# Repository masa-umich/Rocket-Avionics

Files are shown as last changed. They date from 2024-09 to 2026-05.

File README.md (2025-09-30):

# Rocket-Avionics
Embedded firmware for Rocket Avionics

Read Me last updated: 9/2/2025

## Note:
This is a mono-repo meaning that code for the bay boards, flight computer, and all other rocket avionics should go into sub-directories of this repo. The only exception to this is Limewire since that is an interface to the flight computer and not part of rocket avionics itself.

Find all firmware that actually runs on boards in `stm-flight-sw/`

Find all the templates in `stm-templates/`

Sensor Emulation Board (SEB) -> `SEB/`

Apogee Detection Sims & RTOS Threads -> `apogee-detection/`

All on-board driver firmware -> `board-drivers/`

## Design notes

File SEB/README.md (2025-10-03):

# Sesnor Emulation Board Firmware & Software
Author: Jack Hammerberg\
Last updated: 10/2/2025

## Application Notes
* You MUST use hardware NSS when configuring a SPI slave in STM32! The software option will not allow the MISO register to get shifted out
* If re-using the MS5611 emulator code, remember to call `emulation_init()` before your main loop, `emulation_loop(<serial uart>)` in the main loop, and setup SPI interrupts w/ HAL calls disabled and replaced with `emulation_IRQHandler(<spi bus>)`

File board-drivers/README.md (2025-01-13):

# Flight Computer & Bay Board Drivers

## Current Members:
Jack Hammerberg, Felix Foreman, Ryan Salehi

## Summary:
This directory contains all of the relevant drivers used on the rocket avionics firmware. Not every board will use every driver, these drivers are designed to be copy-pasted into each application or project as needed. Most if not all require FreeRTOS to work properly for non-blocking opperation.

## Drivers:
* Name: FCBBADC (Flight Computer & Bay Board Analog to Digital Converter)
* Init ADCs in batch
* Read in batch
* Convert to raw in batch
* Convert to voltages in batch (float32 array)
* Driver Functions:
    * Init
    * Get Raw Values
    * Get Raw Voltages
    * Get Voltages & Timestamps

* MAX11128
    * [MAX11128 Datasheet](https://www.analog.com/media/en/technical-documentation/data-sheets/MAX11120-MAX11128.pdf)
    * Type: ADC
    * Interface: SPI
    * Driver Requirements:
        * Init
        * Send Command
        * Read Register
        * Write Register
        * Get Voltage

* LPS22HBTR 
    * [LPS22HBTR Datasheet](https://www.st.com/content/ccc/resource/technical/document/datasheet/bf/c1/4f/23/61/17/44/8a/DM00140895.pdf/files/DM00140895.pdf/jcr:content/translations/en.DM001408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)
    * Type: Barometer/Altimeter 
    * Interface: SPI
    * Driver Requirements:
        * Init
        * Send Command
        * Read Register
        * Write Register
        * Get Altitude
        * Get Pressure

* LSM6DSO32XTR
    * [LSM6DSO32XTR Datasheet](https://www.st.com/resource/en/datasheet/lsm6dso32x.pdf)
    * Type: IMU
    * Interface: SPI
    * Driver Requirements:
        * Init
        * Send Command
        * Read Register
        * Write Register
        * Get Accelleration
        * Get Angular Rate
        * Get Temperature

* M5611
    * [M5611 Datasheet](https://www.mouser.com/datasheet/2/418/6/ENG_DS_MS5611_01BA03_B3-1134567.pdf)
    * Type: Barometer/Altimeter
    * Interface: SPI
    * Driver Requirements:
        * Init
        * Pressure Convert
        * Temperature Convert
        * Read Pressure
        * Read Temperature

* M24256E
    * [M24256E Datasheet](https://www.st.com/resource/en/datasheet/m24256e-f.pdf)
    * Type: EEPROM 
    * Interace: I2C
    * Driver Requirements:
        * Init
        * Send Command
        * Read Register
        * Write Register
        * Write Flash
        * Read Flash

* NEO-M9N-00B
    * [NEO-M9N-00B](https://content.u-blox.com/sites/default/files/NEO-M9N-00B_DataSheet_UBX-19014285.pdf)
    * Type: GPS
    * Interface: SPI
    * Driver Requirements:
        * Init
        * Send Command
        * Read Register
        * Write Register
        * Get Lat/Long/Alt

* SX1280 
    * [SX1280 Datasheet](https://semtech.my.salesforce.com/sfc/p/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)
    * Type: LoRa 2.4GHz Radio 
    * Interface: SPI
    * Driver Requirements:
        * Init
        * Send Command
        * Read Register
        * Write Register
        * Transmit Data
        * Recieve Data

* W25N01GVZEIG
    * [W25N01GV Datasheet](https://www.winbond.com/resource-files/w25n01gv%20revl%20050918%20unsecured.pdf)
    * Type: Flash 
    * Interface: SPI
    * Driver Requirements:
        * Init
        * Send Command
        * Read Register
        * Write Register
        * Write Flash
        * Read Flash

* ADS1120 
    * [ADS1120 Datasheet](https://www.ti.com/lit/ds/symlink/ads1120.pdf)
    * Type: Thermocouple ADC
    * Interface: SPI
    * Driver Requirements:
        * Init
        * Send Command
        * Read Register
        * Write Register
        * Get Temperature
        * Read All TCs and Attach Timestamps

* Valves
    * Type: Solenoid Valves
    * Interface: GPIO & Shift Register
    * Driver Requirements:
        * Valve Voltage Config (Shift Register)
        * Open Valve
        * Close Valve

* TCP
    * Type: TCP/IP
    * Interface: Ethernet
    * Driver Requirements:
        * Packet Parsing
        * Connection Thread Manager
        * TCP Server
        * TCP Client

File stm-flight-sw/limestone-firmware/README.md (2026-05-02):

# Limestone Firmware
Author: Felixfb, Jackmh </br>
Read Me last updated: 12/8/2025

## Note:
This is the location for the flight computer firmware for Limelight. This README will be
updated more as the firmware is written. The firmware currently works and has been
lightly tested on the system. Shakedown approved!

## Important Notes:
Major STM32 bug: the EthIf task does not get enough stack by default, you must go into the ethernetif.c file and change the INTERFACE_THREAD_STACK_SIZE definition at the top from 350 to anything above 380 (I would pick 500 to be safe). If this is not done, the task will start corrupting memory as soon as it starts.

Major STM32 LAN8742 driver bug: The Ethernet link output does not free sent TX packets
until the TX descriptors have run out of space. One fix is to add a task that waits on the
tx buffer semaphore and clears the descriptors of sent packets every time the LAN chip
triggers a TX complete. See ethernetif.c ethernet_patch(), along with the initialization
of the task in low_level_init() for an example.

## Versioning
To keep track of the firmware version, a header file with build information is
auto-generated before each build. This build
information includes the short hash of the most recent git commit, the active branch, type
of build (Debug vs Release), and the timestamp of the build. This build info is logged in
flash and over UDP when the firmware starts. The auto-generation script is a [uv
script](../version-info/version-gen.py) that the STM32
project is set up to automatically try to install uv and run the script before a build. The configuration assumes that uv is installed in
~/.local/bin/uv (this is the default install location), but if your uv is installed in a different location, you can go to
Properties -> C/C++ Build -> Environment and add the location of your uv to the PATH
variable.

## Networking Structure
The networking for Limelight's avionics can be split into 3 main pieces:
- Telemetry is encoded using LMP and broadcasted over UDP port 6767
- Event logs are broadcasted over UDP port 1234, encoded as raw strings
- Valve and board control is done over a TCP network on port 5000. The flight computer
  acts as the TCP server, while the other boards and the EBox act as TCP clients. All
  messages over this network are encoded according to LMP. 

[LMP reference](http://masa.eecs.umich.edu/wiki/index.php/Limelight_TCP_Message_Structure)

## EEPROM Data Ordering

| Byte  | Meaning | C data type |
| :-----: | --- | :---: |
| 1 - 4 | PT 1 Voltage Offset | float |
| 5 - 8 | PT 1 Pressure Range | float |
| 9 - 12 | PT 1 Maximum Voltage | float |
| 13 - 16 | PT 2 Voltage Offset | float |
| 17 - 20 | PT 2 Pressure Range | float |
| 21 - 24 | PT 2 Maximum Voltage | float |
| 25 - 28 | PT 3 Voltage Offset | float |
| 29 - 32 | PT 3 Pressure Range | float |
| 33 - 36 | PT 3 Maximum Voltage | float |
| 37 - 40 | PT 4 Voltage Offset | float |
| 41 - 44 | PT 4 Pressure Range | float |
| 45 - 48 | PT 4 Maximum Voltage | float |
| 49 - 52 | PT 5 Voltage Offset | float |
| 53 - 56 | PT 5 Pressure Range | float |
| 57 - 60 | PT 5 Maximum Voltage | float |
| 61 | TC 1 Gain | uint8_t |
| 62 | TC 2 Gain | uint8_t |
| 63 | TC 3 Gain | uint8_t |
| 64 | Valve 1 Voltage | uint8_t |
| 65 | Valve 1 Enable | uint8_t |
| 66 | Valve 2 Voltage | uint8_t |
| 67 | Valve 2 Enable | uint8_t |
| 68 | Valve 3 Voltage | uint8_t |
| 69 | Valve 3 Enable | uint8_t |
| 70 - 73 | DAQ PC/Limewire IP | uint32_t |
| 74 - 77 | Flight Computer IP | uint32_t |
| 78 - 81 | Bay Board 1 IP | uint32_t |
| 82 - 85 | Bay Board 2 IP | uint32_t |
| 86 - 89 | Bay Board 3 IP | uint32_t |
| 90 - 93 | Flight Recorder IP | uint32_t |
| 94 | Ox MPV Valve Channel | uint8_t |
| 95 | Fuel MPV Valve Channel | uint8_t |
| 96 | BOP Piston Valve Channel | uint8_t |
| 97 | Drogue Chute Valve Channel | uint8_t |
| 98 | Main Chute Valve Channel | uint8_t |
| 99 | Fuel Dome Iso Channel | uint8_t |
| 100 | Ox Dome Iso Channel | uint8_t |

### Notes
The PT configuration floats are **little-endian**, but the IP addresses are
**big-endian**. The last 5 entries of the EEPROM are 0-indexed, so the first valve channel
would be 0.

TC gain chart:
| Gain | Config Value |
| :---: | :---: |
| 1x | 0x00 |
| 2x | 0x01 |
| 4x | 0x02 |
| 8x | 0x03 |
| 16x | 0x04 |
| 32x | 0x05 |
| 64x | 0x06 |
| 128x | 0x07 |

For the valve voltage configuration, 12V is 0x00, 24V is 0x01

The eeprom config file must named eeprom.bin and must have 32 bit CRC32 checksum at the end of the file of the rest of the config. This 32 bit checksum should be little-endian

You can then send the eeprom.bin using any TFTP client

Refer to [eeprom-bin-generate.py](eeprom-bin-generate.py) for an example or to actually generate a config

## TCP Keep-Alive

Idle timeout - 3 seconds

Probe interval - 1 seconds

Probe count - 3

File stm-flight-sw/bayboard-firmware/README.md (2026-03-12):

# Bay Board Firmware
Author: Felixfb </br>
Read Me last updated: 12/8/2025

## Important Notes:
Major STM32 bug: the EthIf task does not get enough stack by default, you must go into the ethernetif.c file and change the INTERFACE_THREAD_STACK_SIZE definition at the top from 350 to anything above 380 (I would pick 500 to be safe). If this is not done, the task will start corrupting memory as soon as it starts.

Major STM32 LAN8742 driver bug: The Ethernet link output does not free sent TX packets until the TX descriptors have run out of space. One fix is to add a task that waits on the tx buffer semaphore and clears the descriptors of sent packets every time the LAN chip triggers a TX complete. See ethernetif.c ethernet_patch(), along with the initialization of the task in low_level_init() for an example.

## Versioning
To keep track of the firmware version, a header file with build information is
auto-generated before each build. This build
information includes the short hash of the most recent git commit, the active branch, type
of build (Debug vs Release), and the timestamp of the build. This build info is logged in
flash and over UDP
when the firmware starts. The auto-generation script is a [uv
script](../version-info/version-gen.py) that the STM32
project is set up to automatically try to install uv and run the script before a build. The configuration assumes that uv is installed in
~/.local/bin/uv (this is the default install location), but if your uv is installed in a different location, you can go to
Properties -> C/C++ Build -> Environment and add the location of your uv to the PATH variable.

## EEPROM Data Ordering

| Bytes | Meaning | C data type |
| :-----: | --- | :---: |
| 1 | Bay Board # | uint8_t |
| 4 | PT 1 Voltage Offset | float |
| 4 | PT 1 Pressure Range | float |
| 4 | PT 1 Maximum Voltage | float |
| 4 | PT 2 Voltage Offset | float |
| 4 | PT 2 Pressure Range | float |
| 4 | PT 2 Maximum Voltage | float |
| 4 | PT 3 Voltage Offset | float |
| 4 | PT 3 Pressure Range | float |
| 4 | PT 3 Maximum Voltage | float |
| 4 | PT 4 Voltage Offset | float |
| 4 | PT 4 Pressure Range | float |
| 4 | PT 4 Maximum Voltage | float |
| 4 | PT 5 Voltage Offset | float |
| 4 | PT 5 Pressure Range | float |
| 4 | PT 5 Maximum Voltage | float |
| 4 | PT 6 Voltage Offset | float |
| 4 | PT 6 Pressure Range | float |
| 4 | PT 6 Maximum Voltage | float |
| 4 | PT 7 Voltage Offset | float |
| 4 | PT 7 Pressure Range | float |
| 4 | PT 7 Maximum Voltage | float |
| 4 | PT 8 Voltage Offset | float |
| 4 | PT 8 Pressure Range | float |
| 4 | PT 8 Maximum Voltage | float |
| 4 | PT 9 Voltage Offset | float |
| 4 | PT 9 Pressure Range | float |
| 4 | PT 9 Maximum Voltage | float |
| 4 | PT 10 Voltage Offset | float |
| 4 | PT 10 Pressure Range | float |
| 4 | PT 10 Maximum Voltage | float |
| 1 | TC 1 Gain | uint8_t |
| 1 | TC 2 Gain | uint8_t |
| 1 | TC 3 Gain | uint8_t |
| 1 | TC 4 Gain | uint8_t |
| 1 | TC 5 Gain | uint8_t |
| 1 | TC 6 Gain | uint8_t |
| 1 | Valve 1 Voltage | uint8_t |
| 1 | Valve 1 Enable | uint8_t |
| 1 | Valve 2 Voltage | uint8_t |
| 1 | Valve 2 Enable | uint8_t |
| 1 | Valve 3 Voltage | uint8_t |
| 1 | Valve 3 Enable | uint8_t |
| 1 | Valve 4 Voltage | uint8_t |
| 1 | Valve 4 Enable | uint8_t |
| 1 | Valve 5 Voltage | uint8_t |
| 1 | Valve 5 Enable | uint8_t |
| 4 | Flight Computer IP | uint32_t |
| 4 | Bay Board IP | uint32_t |

### Notes
The PT configuration floats are **little-endian**, but the IP addresses are **big-endian**.

The Bay Board # directly corresponds to the board, e.g. Bay Board 1 is 1

TC gain chart:
| Gain | Config Value |
| :---: | :---: |
| 1x | 0x00 |
| 2x | 0x01 |
| 4x | 0x02 |
| 8x | 0x03 |
| 16x | 0x04 |
| 32x | 0x05 |
| 64x | 0x06 |
| 128x | 0x07 |

For the valve voltage configuration, 12V is 0x00, 24V is 0x01

The eeprom config file must named eeprom.bin and must have 32 bit CRC32 checksum at the end of the file of the rest of the config. This 32 bit checksum should be little-endian

You can then send the eeprom.bin using any TFTP client

Refer to [eeprom-bin-generate.py](eeprom-bin-generate.py) for an example or to actually generate a config

## TCP Keep-Alive

Idle timeout - 3 seconds

Probe interval - 1 seconds

Probe count - 3

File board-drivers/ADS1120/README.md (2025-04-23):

# ADS1120 
* [ADS1120 Datasheet](https://www.ti.com/lit/ds/symlink/ads1120.pdf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)
* Type: Temperature
* Interface: SPI2
* Driver Requirements:
    * Init
    * Send Command
    * Read Register
    * Write Register
    * Get Temperature
    * Read All TCs and Attach Timestamps

<br/><br/>

# Contents
 - [SPI Setup](#spisetup)
 - [Example Usage](#usage)
 - [Tips](#tips)
 - [Reference](#ref)
    - [Mux Constants](#mux)
    - [Gain Constants](#gain)
    - [Datarate Constants](#rate)
    - Structs
       - [ADS_Main_t](#mainhand)
       - [ADS_TC_t](#tchand)
       - [ADS_Reading_t](#readingst)
       - [ADS_Chip](#chiphand)
    - Functions
       - [ADS_configTC()](#confTC)
       - [ADS_init()](#init)
       - [ADS_readIndividual()](#read1)
       - [ADS_readIndividualwTimestamp()](#read1t)
       - [ADS_readAll()](#readall)
       - [ADS_readAllwTimestamps()](#readallt)
       - [ADS_readInternalTemp()](#readInt)
       - [ADS_convertRawToMicrovolts()](#convertraw)
       - [ADS_polyMicrovoltsToTemp()](#polymtt)
       - [ADS_polyTempToMicrovolts()](#polyttm)
       - [vTCTask()](#task)
       - [ADS_configure()](#configChip)
       - [ADS_configureChip()](#configChipd)

# SPI Setup

* Frame Format: Motorola
* Data Size: 8 bits
* First Bit: MSB First
* Clock Polarity: Low
* Clock Phase: 2 Edge

# Example Usage

This example sets up 4 thermocouples connected to 2 chips. Both chips are connected to SPI 1 and the MISO pin is set as pin PA_6.

Must define `getTimestamp()` somewhere earlier. This example sets up the timestamp to be the time since startup in milliseconds:
```c
uint64_t getTimestamp() {
	return HAL_GetTick();
}
```

```c
ADS_Main_t main_handle = {0};
ADS_TC_t multiTCs[4]; // Set up 4 thermocouples

// Configure the 4 thermocouple connections.
ADS_configTC(&multiTCs[0], &hspi1, GPIOA, GPIO_PIN_6, 0xffff, SPI2_CS1_GPIO_Port, SPI2_CS1_Pin, ADS_MUX_AIN2_AIN3, ADS_PGA_GAIN_1, ADS_DATA_RATE_20);
ADS_configTC(&multiTCs[1], &hspi1, GPIOA, GPIO_PIN_6, 0xffff, SPI2_CS1_GPIO_Port, SPI2_CS1_Pin, ADS_MUX_AIN1_AIN0, ADS_PGA_GAIN_1, ADS_DATA_RATE_20);
ADS_configTC(&multiTCs[2], &hspi1, GPIOA, GPIO_PIN_6, 0xffff, SPI2_CS2_GPIO_Port, SPI2_CS2_Pin, ADS_MUX_AIN2_AIN3, ADS_PGA_GAIN_1, ADS_DATA_RATE_20);
ADS_configTC(&multiTCs[3], &hspi1, GPIOA, GPIO_PIN_6, 0xffff, SPI2_CS2_GPIO_Port, SPI2_CS2_Pin, ADS_MUX_AIN1_AIN0, ADS_PGA_GAIN_1, ADS_DATA_RATE_20);

// Initialize and start the RTOS task
ADS_init(&main_handle, multiTCs, 4);

// Loop indefinitely, reading from every thermocouple twice a second
for(;;) {
    ADS_Reading_t readings[4];

    int status = ADS_readAllwTimestamps(&main_handle, readings);
    if(!status) {
        // Iterate through the readings. The order will match the order of multiTCs.
        for(int i = 0;i < 4;i++) {
            if(!readings[i].error) {
                // Do something with readings[i].temp_c and readings[i].timestamp
                // Again, the thermocouple that this corresponds to is whichever is index i in multiTCs
            }
            else {
                // Failed to retrieve this thermocouple temperature
            }
        }
    }
    else {
        // Failed to retrieve internal temperature, all readings are invalid
    }

	osDelay(500);
}
```

## Tips

### Picking a datarate/polling rate:
Unfortunately, since the ADS1120 cannot reading from multiple connects at once, this driver has to switch between the connected thermocouples on each chip, causing a lot of delay in between readings. This means that the configured datarate for each thermocouple is not actually how often the reading gets updated in the driver. I'd recommend using a datarate of a little over 2x your desired polling rate. For example, if you need a polling rate of 50Hz, use a datarate of 90Hz if the polling rate isn't super important, 175Hz if the polling rate is very important.

### Understand errors:
If a read function fails to retrieve a reading, it doesn't mean that a new reading isn't ready. Also, you can call the read functions as often as you want, 
if a new reading isn't ready it just returns the previous reading. Basically, whether or not a read function fails has nothing to do with if data is ready on the ADS1120 side.

# Reference

## Mux Constants
`ADS_MUX_AIN0_AIN1` - Positive lead connected to AIN0, negative lead connected to AIN1

`ADS_MUX_AIN0_AIN2` - Positive lead connected to AIN0, negative lead connected to AIN2

`ADS_MUX_AIN0_AIN3` - Positive lead connected to AIN0, negative lead connected to AIN3

`ADS_MUX_AIN1_AIN2` - Positive lead connected to AIN1, negative lead connected to AIN2

`ADS_MUX_AIN1_AIN3` - Positive lead connected to AIN1, negative lead connected to AIN3

`ADS_MUX_AIN2_AIN3` - Positive lead connected to AIN2, negative lead connected to AIN3

`ADS_MUX_AIN1_AIN0` - Positive lead connected to AIN1, negative lead connected to AIN0

`ADS_MUX_AIN3_AIN2` - Positive lead connected to AIN3, negative lead connected to AIN2

## Gain Constants
`ADS_PGA_GAIN_1` - 1x Gain

`ADS_PGA_GAIN_2` - 2x Gain

`ADS_PGA_GAIN_4` - 4x Gain

`ADS_PGA_GAIN_8` - 8x Gain

`ADS_PGA_GAIN_16` - 16x Gain

`ADS_PGA_GAIN_32` - 32x Gain

`ADS_PGA_GAIN_64` - 64x Gain

`ADS_PGA_GAIN_128` - 128x Gain

## Datarate Constants
`ADS_DATA_RATE_20` - 20Hz Polling rate

`ADS_DATA_RATE_45` - 45Hz Polling rate

`ADS_DATA_RATE_90` - 90Hz Polling rate

`ADS_DATA_RATE_175` - 175Hz Polling rate

`ADS_DATA_RATE_330` - 330Hz Polling rate

`ADS_DATA_RATE_600` - 600Hz Polling rate

`ADS_DATA_RATE_1000` - 1000Hz Polling rate

## struct ADS_Main_t

ADS_Main_t is the main handle for everything.
It stores the RTOS task handle for the task that collects thermocouple measurements, pointers to all of the individual thermocouple connections, and the current cold junction temperature.

```c
typedef struct {
	TaskHandle_t tc_task;
	ADS_TC_t *TCs;
	uint8_t TC_count;

	int16_t raw_temp;
	SemaphoreHandle_t temp_semaphore;
	uint32_t last_temp;
} ADS_Main_t;
```

## struct ADS_TC_t

ADS_TC_t stores information about a specific thermocouple connection.
This includes information about the specific ADS1120 chip that the thermocouple is connected to (SPI bus, CS pin), which ADS1120 "channel" it's connected to, and configuration information like the gain and datarate.
It also stores the latest reading and associated timestamp from the thermocouple.

```c
typedef struct {
	SPI_HandleTypeDef* hspi;
	GPIO_TypeDef *DOUT_GPIO_Port;
	uint16_t DOUT_GPIO_Pin;
	uint16_t SPI_TIMEOUT;
	GPIO_TypeDef *CS_GPIO_Port;
	uint16_t CS_GPIO_Pin;
	uint8_t mux;

	uint8_t gain;
	uint8_t rate;
	double step_size;

	int16_t current_raw;
	uint64_t timestamp;
	SemaphoreHandle_t reading_semaphore;
} ADS_TC_t;
```

## struct ADS_Reading_t

ADS_Reading_t packages a single thermocouple reading along with the timestamp when it was read, and an error flag.

`temp_c` is the cold junction compensated temperature in Celsius timestamp is the time when the reading was received from the ADS1120.
It is in whatever format was given by the external function `getTimestamp()`.

If `error` is 0, then `temp_c` and `timestamp` are valid, otherwise there was an issue reading the latest measurement - `temp_c` and `timestamp` will not be valid and could be anything.

```c
typedef struct {
	float temp_c;
	uint64_t timestamp;
	uint8_t error;
} ADS_Reading_t;
```

**Fields:**
 - `temp_c` - The temperature of this reading in Celsius. This is cold junction compensated
 - `timestamp` - The timestamp of this reading. This timestamp corresponds to the time when the reading is received from the ADS1120
 - `error` - The error flag. If this is not 0, then both `temp_c` and `timestamp` are not valid

## struct ADS_Chip

ADS_Chip contains information for each ADS1120 chip.
It stores SPI bus information, pointers to the thermocouples that are connected to the chip, and timing information related to reading from the chip and switching between thermocouple connections.

```c
typedef struct {
	SPI_HandleTypeDef* hspi;
	GPIO_TypeDef *DOUT_GPIO_Port;
	uint16_t DOUT_GPIO_Pin;
	uint16_t SPI_TIMEOUT;
	GPIO_TypeDef *CS_GPIO_Port;
	uint16_t CS_GPIO_Pin;

	ADS_TC_t* muxes[2];
	uint8_t last_state;
	uint8_t mux_count;
	uint8_t current_mux;
	uint32_t last_tick;
	uint32_t timer_start;
} ADS_Chip;
```

## void ADS_configTC(ADS_TC_t *ADSTC, SPI_HandleTypeDef *hspi, GPIO_TypeDef *DOUT_GPIO_Port, uint16_t DOUT_GPIO_Pin, uint16_t SPI_TIMEOUT, GPIO_TypeDef *CS_GPIO_Port, uint16_t CS_GPIO_Pin, uint8_t mux, uint8_t gain, uint8_t rate)

Configure a thermocouple with connection information, gain, and datarate.

The DOUT (MISO) pin of the SPI bus is needed since it's used as a GPIO pin 
between SPI communications to determine if data is ready.

NOTE: this does not actually communicate with the chip, it just sets up the struct.

```c
void ADS_configTC(ADS_TC_t *ADSTC, SPI_HandleTypeDef *hspi, GPIO_TypeDef *DOUT_GPIO_Port, uint16_t DOUT_GPIO_Pin, uint16_t SPI_TIMEOUT, GPIO_TypeDef *CS_GPIO_Port, uint16_t CS_GPIO_Pin, uint8_t mux, uint8_t gain, uint8_t rate)
```

**Params:**

- `ADSTC` - The thermocouple to configure
- `hspi` - The SPI handle that the corresponding ADS1120 is connected to
- `DOUT_GPIO_Port` - The GPIO port that the MISO pin of the SPI bus is connected to
- `DOUT_GPIO_Pin` - The GPIO pin that the MISO pin of the SPI bus is connected to
- `SPI_TIMEOUT` - The timeout to use for SPI communications (milliseconds)
- `CS_GPIO_Port` - The GPIO port that the chip select pin of the ADS1120 is connected to
- `CS_GPIO_Pin` - The GPIO pin that the chip select pin of the ADS1120 is connected to
- `mux` - The combination of pins on the ADS1120 that the thermocouple is connected to.
- `gain` - The gain to use for this thermocouple
- `rate` - The datarate to use for this thermocouple

## int ADS_init(ADS_Main_t *ADSMain, ADS_TC_t *TCs, uint8_t num_TCs)

Configure the main struct and initialize the RTOS task.

```c
int ADS_init(ADS_Main_t *ADSMain, ADS_TC_t *TCs, uint8_t num_TCs)
```

**Params:**

- `ADSMain` - The main handle where the RTOS task handle and all thermocouple pointers should be stored
- `TCs` - The thermocouples to be monitored by the RTOS task. This should be a pointer to an array of thermocouples
- `num_TCs` - The number of thermocouples to be monitored by the RTOS task

**Returns:**

- The status of the created RTOS task. Returns 0 if the task started successfully, returns 1 if the task failed to start

## int ADS_readIndividual(ADS_Main_t *ADSMain, uint8_t TC_index, float *reading)

Get the latest temperature of one thermocouple.
This reading is cold junction compensated using one of the connected ADS1120s.

```c
int ADS_readIndividual(ADS_Main_t *ADSMain, uint8_t TC_index, float *reading)
```

**Params:**

- `ADSMain` - The main driver handle
- `TC_index` - The index of the thermocouple to be read. This is 0 indexed and is based on the order of the array that was originally passed to `ADS_init`
- `reading` - The pointer to where the reading should be stored. This is a temperature measurement in Celsius

**Returns:**

- Returns 0 if retrieving the reading was successful, returns 1 if the reading could not be retrieved

## int ADS_readIndividualwTimestamp(ADS_Main_t *ADSMain, uint8_t TC_index, ADS_Reading_t *reading)

Get the latest temperature of one thermocouple, including the timestamp when it was collected.
This reading is cold junction compensated using one of the connected ADS1120s.

The error flag in the passed ADS_Reading_t reflects the success of this function, and either it or the return value can be used to determine whether or not the function successfully retrieved the reading.

The timestamp of the reading is taken when the reading is received from the ADS1120 NOT when this function is called. This means it can be 
used to determine if everything is working and readings are being updated. For example, if the datarate is set at 20Hz, and the timestamp is significantly greater than 50ms in the past, the reading is probably not getting updated.

```c
int ADS_readIndividualwTimestamp(ADS_Main_t *ADSMain, uint8_t TC_index, ADS_Reading_t *reading)
```

**Params:**

- `ADSMain` - The main driver handle
- `TC_index` - The index of the thermocouple to be read. This is 0 indexed and is based on the order of the array that was originally passed to `ADS_init`
- `reading` - The pointer to where the reading should be stored. This is a temperature measurement in Celsius

**Returns:**

- Returns 0 if retrieving the reading was successful, returns 1 if the reading could not be retrieved

## int ADS_readAll(ADS_Main_t *ADSMain, float *readings)

Get the latest temperature of all thermocouples.
These readings are cold junction compensated using one of the connected ADS1120s.

Readings are in the order that their corresponding thermocouple was passed to `ADS_init`.

If a reading couldn't be retrieved, its reading will be NAN.
Even if this function returns 0, some or all of the readings could not have been retrieved. The individual readings will reflect if they weren't successful (NAN). If this function returns 1, then all readings are not valid.

```c
int ADS_readAll(ADS_Main_t *ADSMain, float *readings)
```

**Params:**

- `ADSMain` - The main driver handle
- `readings` - The pointer to the array where the readings should be stored. This should be at least as long as the number of thermocouples that were passed to `ADS_init`

**Returns:**

- Returns 0 if retrieving the internal temperature was successful, returns 1 if the internal temperature could not be retrieved

## int ADS_readAllwTimestamps(ADS_Main_t *ADSMain, ADS_Reading_t *readings)

Get the latest temperature of all thermocouples.
These readings are cold junction compensated using one of the connected ADS1120s.

Readings are in the order that their corresponding thermocouple was passed to `ADS_init`.

If a reading couldn't be retrieved, its error flag will be 1.
Even if this function returns 0, some or all of the readings could not have been retrieved. The individual readings will reflect if they weren't successful (error flag = 1). If this function returns 1, then all readings are not valid, although their error flags might not reflect this.

Just as in `ADS_readIndividualwTimestamp()`, the timestamps are taken when the readings are received from the ADS1120s, so they can be used to determine if readings are being updated.

```c
int ADS_readAllwTimestamps(ADS_Main_t *ADSMain, ADS_Reading_t *readings)
```

**Params:**

- `ADSMain` - The main driver handle
- `readings` - The pointer to the array where the readings and timestamps should be stored. This should be at least as long as the number of thermocouples that were passed to `ADS_init`

**Returns:**

- Returns 0 if retrieving the internal temperature was successful, returns 1 if the internal temperature could not be retrieved

## int ADS_readInternalTemp(ADS_Main_t *ADSMain, float *temp)

Get the latest internal temperature from one of the ADS1120s.
By default this is updated twice a second, but it can be changed by changing the `ADS_INTERNAL_TEMP_DELAY` macro.
This is the temperature used for cold junction compensation in all read functions. The specific ADS1120 that this is retrieved from is whichever ADS1120 is connected to the first thermocouple passed to `ADS_init`.

```c
int ADS_readInternalTemp(ADS_Main_t *ADSMain, float *temp)
```

**Params:**

- `ADSMain` - The main driver handle
- `temp` - The pointer to where the temperature should be stored. This temperature is in Celsius

**Returns:**

- Returns 0 if retrieving the temperature was successful, returns 1 if it could not be retrieved

## double ADS_convertRawToMicrovolts(ADS_TC_t *ADS, int16_t raw)

Convert a raw 16 bit value from a ADS1120 to a microvolt reading.

```c
double ADS_convertRawToMicrovolts(ADS_TC_t *ADS, int16_t raw)
```

**Params:**

- `ADS` - The thermocouple that this reading came from
- `raw` - The 16 bit value from the ADS1120

**Returns:**

- The voltage measured by the ADS1120 in microvolts

## float ADS_polyMicrovoltsToTemp(double microvolts)

Convert a voltage of a type T thermocouple to its corresponding temperature.

```c
float ADS_polyMicrovoltsToTemp(double microvolts)
```

**Params:**

- `microvolts` - The voltage of the thermocouple in microvolts

**Returns:**

- The calculated temperature of the thermocouple in Celsius

## double ADS_polyTempToMicrovolts(float temp)

Convert the temperature of a type T thermocouple to the voltage it would read.

```c
double ADS_polyTempToMicrovolts(float temp)
```

**Params:**

- `temp` - The temperature of the thermocouple in Celsius

**Returns:**

- The calculated voltage in microvolts that the thermocouple should generate if it was at the given temperature

## void vTCTask(void *pvParameters)

The main function for the RTOS task.
Collects and stores readings from all thermocouples, including a cold junction temperature from one of the connected ADS1120s.

```c
void vTCTask(void *pvParameters)
```

**Params:**

- `pvParameters` - The pointer to the main ADS_Main_t handle

## int ADS_configure(ADS_Chip *ADS, uint8_t TC_index, int check)

Configure an ADS1120 to read from one of its connected thermocouples.
This can also be used to configure an ADS1120 to read from its internal temperature sensor.

```c
int ADS_configure(ADS_Chip *ADS, uint8_t TC_index, int check)
```

**Params:**

- `ADS` - The specific ADS1120 chip to configure
- `TC_index` - The index of the thermocouple to set up the ADS1120 to read from. This is specific to how the ADS chip struct was set up, and since there can be up to 2 thermocouples connected to each chip, this parameter can only be 0 or 1. If this parameter is 2, the ADS1120 is configured to read from its internal temperature sensor
- `check` - If this is 1, the configuration of the ADS1120 will be checked after it's written to make sure the new configuration was saved. If this is 0, no verification is done

**Returns:**

- The result of the verification. Returns 0 if the verification passes and the configuration on the ADS1120 matches the passed configuration and returns 1 if the configuration fails and the ADS1120 configuration remains the same as before this function was called. If check is 0, then this always returns 0

## int ADS_configureChip(ADS_Chip *ADS, int check)

Configure an ADS1120 chip with the default configuration

```c
int ADS_configureChip(ADS_Chip *ADS, int check)
```

**Params:**

- `ADS` - The specific ADS1120 chip to configure
- `check` - If this is 1, the configuration of the ADS1120 will be checked after it's written to make sure the new configuration was saved. If this is 0, no verification is done

**Returns:**

- The result of the verification. Returns 0 if the verification passes and the configuration on the ADS1120 matches the passed configuration and returns 1 if the configuration fails and the ADS1120 configuration remains the same as before this function was called. If check is 0, then this always returns 0

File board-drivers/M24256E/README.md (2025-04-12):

# M24256E
* [M24256E Datasheet](https://www.st.com/resource/en/datasheet/m24256e-f.pdf)
* Type: EEPROM 
* Interace: I2C
* Driver Requirements:
    * Init
    * Send Command
    * Read Register
    * Write Register
    * Write Flash
    * Read Flash

## Dev Board Pinout

NOTE: The SO8N package for this IC doesn't have a
physical indicator for where Pin 1 is. I assumed that
the writing in the drawing in Section 10.1 of the
datasheet is the same orientation as the writing on
the IC itself.

| Pin # | Function |
|---|---|
| 1 | NC |
| 2 | NC |
| 3 | NC |
| 4 | VSS |
| 5 | SDA |
| 6 | SCL |
| 7 | !WC |
| 8 | VCC |

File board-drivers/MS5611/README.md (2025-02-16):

# MS5611 Driver
README Last Updated: 2/16/2025

Primary Author: Jackmh

## Overview
This is a driver for the secondary barometer, the MS5611, used to read pressure and derive altitude.

## Example usage:
```c
  MS5611 bar;
  bar.hspi = &hspi3;
  bar.SPI_TIMEOUT = 100;
  bar.CS_GPIO_Port = GPIOD; // PD2
  bar.CS_GPIO_Pin = GPIO_PIN_2;
  bar.pres_offset = 0;
  bar.alt_offset = 0;

  MS5611_PROM_t prom;
  prom.constants.C1 = 0;
  prom.constants.C2 = 0;
  prom.constants.C3 = 0;
  prom.constants.C4 = 0;
  prom.constants.C5 = 0;
  prom.constants.C6 = 0;

  MS5611_Reset(&bar);
  MS5611_readPROM(&bar, &prom);

  float pres = 0.0;
  float alt = 0.0;

  /* Infinite loop */
  for(;;) {
    MS5611_getPres(&bar, &pres, &prom, OSR_256);
    MS5611_getAlt(&bar, &alt, &prom, OSR_256); // Altitude from sea-level in feet
    osDelay(500);
  }
```

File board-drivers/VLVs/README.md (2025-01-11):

# Valve Driver
README Last Updated: 1/11/2025

Primary Author: Jackmh

## Overview
This driver is used to control valves on the board. This includes control of the shift register (SN74LV164A), a wrapper of HAL GPIO functions for toggling digital pins, and control MOSFETS attached to the valve channels.

## Example usage:
```c
Shift_Reg reg = {0};
reg.VLV_CTR_GPIO_Port = GPIOA;
reg.VLV_CTR_GPIO_Pin = VLV_CTRL_Pin;
reg.VLV_CLK_GPIO_Port = GPIOA;
reg.VLV_CLK_GPIO_Pin = BUFF_CLK_Pin;
reg.VLV_CLR_GPIO_Port = GPIOA;
reg.VLV_CLR_GPIO_Pin = BUFF_CLR_Pin;

Valve VLV1 = {0};
VLV1.VLV_EN_GPIO_Port = GPIOC;
VLV1.VLV_EN_GPIO_Pin = VLV_EN1_Pin;

VLV_Set_Voltage(reg, 0b01000000);
for (;;) {
    VLV_Toggle(VLV1);
    HAL_GPIO_TogglePin(GPIOE, LED_BLUE_Pin);
    osDelay(1000);
}
```

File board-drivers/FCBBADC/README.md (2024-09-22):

## ADC Drivers:
* Name: FCBBADC (Flight Computer & Bay Board Analog to Digital Converter)
* Read in batch
* Convert to raw in batch
* Convert to voltages in batch (float32 array)
* Driver Functions:
    * `readADCRaw()`
		* Get Raw Values
		* Parameters: 
			* `ADC_HandleTypeDef*` for your ADC type handler
			* `int` for the amount of channels you are using
			* `int*` for the array you want values in
			* `int` for the maximum delay per channel in milliseconds
    * `readADCVolt()`
		* Get Raw Voltages
		* Parameters: 
			* `ADC_HandleTypeDef*` for your ADC type handler
			* `int` for the amount of channels you are using
			* `float*` for the array you want values in
			* `int` for the maximum delay per channel in milliseconds
    * `readADC()`
		* Get Voltages & Timestamps
		* Parameters: 
			* `ADC_HandleTypeDef*` for your ADC type handler
			* `int` for the amount of channels you are using
			* `float*` for the array you want ADC values in & timestamp
			* `int` for the maximum delay per channel in milliseconds
## Important Usage Information
To setup multiple channels to read, in your CubeIDE IOC file, you must enable `Scan Conversion Mode` by increasing `Number of Conversion` under `ADC_Regular_ConversionMode` to the amount of channels you will be using. You must also enable `Discontinuous Conversion Mode` and set `Number of Discontinuous Conversions` to the same number of ranks you configured.

Due to how multi-channel ADCs work, you must increase `Sampling Time` for each rank you create to a value equal to or more than `64.5`. If using standard clocks, this means that each channel takes about **3 microseconds** to read, so keep that in mind when using this.

This driver assumes there is a function called `getTimestamp()` that returns a uint64_t somewhere else in the program. An example of this can be [found below](#example-gettimestamp-function) 
## Example Usage
```c
TickType_t xLastWakeTime;
const TickType_t xFrequency = 750; // Milliseconds
// Initialize the xLastWakeTime variable with the current time.
xLastWakeTime = xTaskGetTickCount();
int channels = 4;
// Must be one larger than the number of channels to include the timestamp
// Can be equal to amount of channels if using readADCRaw() or readADCVolt()
float adcValues[5];

for(;;) {
	vTaskDelayUntil(&xLastWakeTime, xFrequency);
	readADC(&hadc1, channels, adcValues, HAL_MAX_DELAY);
	HAL_GPIO_TogglePin(GPIOB, GPIO_PIN_14); //LED
}
```
***
## Example getTimestamp() Function
In the future, we will need a timestamp function with sub-millisecond timing but an external `getTimestamp()` function is required, so here is an example.
```c
uint64_t getTimestamp(void) {
	uint32_t timestamp = HAL_GetTick();
	return (uint64_t)timestamp;
}
```

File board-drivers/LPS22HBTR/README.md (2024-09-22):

# LPS22HBTR 
* [LPS22HBTR Datasheet](https://www.st.com/content/ccc/resource/technical/document/datasheet/bf/c1/4f/23/61/17/44/8a/DM00140895.pdf/files/DM00140895.pdf/jcr:content/translations/en.DM001408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)
* Type: Barometer/Altimeter 
* Interface: SPI1
* Driver Requirements:
    * Init
    * Send Command
    * Read Register
    * Write Register
    * Get Altitude
    * Get Pressure

Example Usage:

```C
  /* USER CODE BEGIN 5 */
  /* Infinite loop */
  TickType_t xLastWakeTime;
  const TickType_t xFrequency = 100; //Milliseconds
  xLastWakeTime = xTaskGetTickCount();
  float Pres = 0.0;
  float Temp = 0.0;

  BAR BAR1 = {0};
  BAR1.hspi = &hspi6;
  BAR1.SPI_TIMEOUT = 1000;
  BAR1.CS_GPIO_Port = GPIOA;
  BAR1.CS_GPIO_Pin = GPIO_PIN_4;
  BAR1.pres_offset = 0;
  BAR1.alt_offset = 0;

  if (BAR_init(&BAR1)) {
	  Error_Handler(); //We have not read the who am I register, so something is probably wrong
  }

  for(;;) {
	  vTaskDelayUntil(&xLastWakeTime, xFrequency);
      BAR_getPres(&BAR1, &Pres);
      BAR_getTemp(&BAR1, &Temp);
  }
```

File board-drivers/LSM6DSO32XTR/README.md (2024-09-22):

# LSM6DSO32XTR
* [LSM6DSO32XTR Datasheet](https://www.st.com/resource/en/datasheet/lsm6dso32x.pdf)
* Type: IMU
* Interface: SPI1
* Driver Requirements:
    * Init
    * Send Command
    * Read Register
    * Write Register
    * Get Accelleration
    * Get Angular Rate
    * Get Temperature

***
I'll make this better later, but here's some example code:
```c
	TickType_t xLastWakeTime;
	const TickType_t xFrequency = 1; //Milliseconds
	// Initialize the xLastWakeTime variable with the current time.
	xLastWakeTime = xTaskGetTickCount();
	float temp;

	AngRate G_readings = {0};
	G_readings.G_x = 0;
	G_readings.G_y = 0;
	G_readings.G_z = 0;

	Accel XL_readings = {0};
	XL_readings.XL_x = 0;
	XL_readings.XL_y = 0;
	XL_readings.XL_z = 0;

	IMU IMU1;
	IMU1.hspi = &hspi1;
	IMU1.SPI_TIMEOUT = 9999;
	IMU1.CS_GPIO_Port = GPIOA;
	IMU1.CS_GPIO_Pin = 4;
	IMU1.XL_x_offset = 0;
	IMU1.XL_y_offset = 0;
	IMU1.XL_z_offset = 0;
	IMU1.G_x_offset = 0;
	IMU1.G_y_offset = 0;
	IMU1.G_z_offset = 0;

	IMU_init(&IMU1);
    
	for(;;) {
	  vTaskDelayUntil(&xLastWakeTime, xFrequency);
	  IMU_getAccel(&IMU1, &XL_readings);
	  IMU_getTemp(&IMU1, &temp);
	  IMU_getAngRate(&IMU1, &G_readings);
	  HAL_GPIO_TogglePin(GPIOB, GPIO_PIN_14); //LED
	}
```

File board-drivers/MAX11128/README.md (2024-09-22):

# UPDATE: Feburary 16th, 2024
* RTOS-ified this (added like 4 lines to pause interupts)
* Pending testing
# User Guide (LAST UPDATED: July 7, 2021)

* [MAX11128 Technical Datasheet](https://datasheets.maximintegrated.com/en/ds/MAX11120-MAX11128.pdf)
* [MAX11131BOB Breakout Board Datasheet](https://datasheets.maximintegrated.com/en/ds/MAX11131BOB.pdf) (Left because MAX11131 is very similar to MAX11128 but does not support not having EOC nor CNVST)

Important note for MAX11131BOB breakout board users: the MAX11131BOB dev board 
connects analog input 15 to REF- by default. To configure it to use AIN15, cut the
jumper J15 and apply analog input at header H2. This can be found on the datasheet
on the [MAX11131BOB datasheet.](https://datasheets.maximintegrated.com/en/ds/MAX11131BOB.pdf)

## Pin Terminology

* CNVST   - ADC pin that is used for starting conversions on the MAX11131 chip
* EOC     - ADC pin set by the MAX11131 chip that tells the microcontroller when
            conversions are ready to be read

### Microcontroller Clock Settings

To guarantee proper functionality, the clock speed on the microcontroller should 
not be set higher than 180 MHz. This is because this library using a noop instruction
to delay execution of the CNVST pin cycle for at least 5ns. This delay is necessary
to guarantee that the ADC properly registers that the CNVST pin has been cycled.

### Configuring SPI settings

The maximum SPI frequency allowed for this ADC is 40 MHz. In the STM32CubeIde
SPI configuration, the configuration settings should be identical to those below. Note: the prescaler is not noted below but should be adjusted accordingly

* Frame Format: Motorola
* Data Size: 8 bits
* First Bit: MSB First
* Clock Polarity: High
* Clock Phase: 2 Edge

### Configuring ADC pins

For this ADC, we need to configure three pins on the microcontroller: EOC, CNVST, and CS. These pins may be on any GPIO pin, but they must be configured exactly as shown below.

CS: (Output pin)
* GPIO output level: High
* GPIO mode: Output Push Pull
* GPIO Pull-up/Pull-down: None
* Maximum output speed: High

CNVST: (Output pin)
* GPIO output level: High
* GPIO mode: Output Push Pull
* GPIO Pull-up/Pull-down: None
* Maximum output speed: High

EOC: (Input pin)
* GPIO mode: Input mode
* GPIO Pull-up/Pull-down: None

### Configuring Hardware Pinouts
1. Initialize `GPIO_MAX11128_Pinfo` struct, this is your main interface for 
    configuring ADC hardware pins and which channels to read from
2. Manually assign pins in `GPIO_MAX11128_Pinfo` to hardware pins. A snippet of 
    the underlying data structure can be found below. For instance, MAX11131_CS_ADDR
    indicates that it is CS pin addr for an ADC.
3. To initialize multiple ADCs, create an array of `GPIO_MAX11128_Pinfo` structs
    and manually assign each struct's pinouts.
4. For future reference, you must provide the pin data for each ADC everytime 
    you want to interface with the ADC.
5. Set `HARDWARE_CONFIGURATION` to `EOC_AND_CNVST`, `EOC_ONLY`, or `NO_EOC_NOR_CNVST` in `GPIO_MAX11128_Pinfo` 

```
typedef struct GPIO_MAX11128_Pinfo {
    GPIO_TypeDef* MAX11128_CS_PORT;     // PORT belonging to CS pin
    GPIO_TypeDef* MAX11128_EOC_PORT;    // PORT belonging to EOC pin
    GPIO_TypeDef* MAX11128_CNVST_PORT;  // PORT belonging to CNVST pin
    uint16_t MAX11128_CS_ADDR;          // PIN belonging to CS pin
    uint16_t MAX11128_EOC_ADDR;         // PIN belonging to EOC pin
    uint16_t MAX11128_CNVST_ADDR;       // PIN belonging to CNVST pin

    uint8_t NUM_CHANNELS;               // Number of channels to read from
    uint8_t MAX11128_CHANNELS[16];      // Channel Identification Numbers

    uint8_t HARDWARE_CONFIGURATION;     // EOC and CNVST pin configuration
} GPIO_MAX11128_Pinfo;
```
3. Once ADC settings are configured, call `init_adc(SPI_HandleTypeDef* SPI_BUS, GPIO_MAX11128_Pinfo *pins)` on each ADC struct, making sure to pass the correct `SPI BUS`, `GPIO_MAX11128_Pinfo` configuration variable. This initializes, by default, 
channels 0-13,15. Channel 14 is not initialized because it will be used for the
CNVST pin in the Custom Internal Mode. Therefore, channel 14 will always read 0. If using MAX11128 in NO_EOC_NOR_CNVST, then all channels will be read.

4. To read current ADC values, call `read_adc(SPI_HandleTypeDef *SPI_BUS, GPIO_MAX11128_Pinfo *pinfo, uint16_t* adc_out)`. The adc_out array that you pass 
in must be of size 16 to guarantee proper behavior. Keep in mind that because
this function requires more than one SPI communication, it is should only be 
called as needed. It requires ~1ms to complete after testing.

5. If you want to change what channels are included in the conversion sequence when using EOC and/or CNVST,
simply modify the `GPIO_MAX11128_Pinfo` configuration struct with the desired 
pinouts and call`void set_read_adc_range(SPI_HandleTypeDef *SPI_BUS, GPIO_MAX11128_Pinfo *pinfo)`. This function also requires more than one SPI communication, and 
should be used on the fly. If unique sets of adc channels are required often,
consider implementing the SampleSet or Manual ADC read procedures. Information
on how to do so is specified in the MAX11128 datasheet linked at the top of this
document. If using no EOC nor CNVST pins, then the loop in read_adc will have to be changed to send the ADC the right channels. See Manual ADC read procedures for more information.

### Sample ADC Initialization Code

Here is all of the sample code needed to read from channels 0-13, 15 on an adc
that is connected to SPI 1. The pin assignment names are macros assigned 
by STM32CubeIDE to the actual micro pins. The `hspi1` is the default name that
STM32CubeIDE declared the SPI 1 bus as. It is officially declared in main.c as `SPI_HandleTypeDef hspi1` and should be auto generated for you after
configuring SPI_x. More information on how to configure SPI can be found [here.](https://www.youtube.com/watch?v=eFKeNPJq50g&feature=emb_title)

```
MX_SPI1_Init();                 // initializes SPI1
uint16_t adc_values[16] = {0};  // array for receiving adc conversions

GPIO_MAX11131_Pinfo adc_pins;
adc_pins.MAX11131_CS_PORT 		= SPI_ADC0_CS_GPIO_Port;
adc_pins.MAX11131_EOC_PORT		= SPI_EOC_GPIO_Port;
adc_pins.MAX11131_CNVST_PORT	= SPI_CNVST_GPIO_Port;
adc_pins.MAX11131_CS_ADDR 		= SPI_ADC0_CS_Pin;
adc_pins.MAX11131_EOC_ADDR		= SPI_EOC_Pin;
adc_pins.MAX11131_CNVST_ADDR	= SPI_CNVST_Pin;
adc_pins.HARDWARE_CONFIGURATION = EOC_ONLY;

init_adc(&hspi1, &adc_pins);

read_adc(&hspi1, &adc_pins, adc_values);
```

# Developer Guide

### Test Procedure (From MAX11131, needs adjustment for MAX11128)

To verify that adc channels 0-13, 15 are working correctly in Custom Internal mode, 
repeat the following procedure below. It is important to note that the MAX11131BOB 
connects analog input 15 to REF- by default. To configure it to use AIN15, cut the
jumper J15 and apply analog input at header H2. This can be found on the datasheet
on the [MAX11131BOB datasheet.](https://datasheets.maximintegrated.com/en/ds/MAX11131BOB.pdf)

1. Setup a timer based interrupt that counts up and is triggered every 1-2 seconds.
2. In the timer interrupt handler, toggle as many output pins from the main
    microcontroller to each ADC_in pin. Ideally, adjacent pins should be configured
    to always have opposite states. In addition, I voltage divided some of the 
    pins and determined roughly what counts I should be expecting for those pins.
3. Initialize the microcontroller to read from channels 0-13, 15 on the ADC.
    Additionally, it is helpful to initialize the ADC values array as a global var 
    in order to view from the live expressions tab in STM32CubeIDE. More information 
    on how to setup live expressions can be found at this [link.](https://www.youtube.com/watch?v=Nyml66k_Ppk)
4. Observe that each adc value in the array match what is expected. Note: the adc
    values are currently in counts, so some additional conversions may be needed.

For a brief example of what this implementation looks like on the Nucleo F446RE 
dev board, I have created an example program below that demonstrates the procedure
on adc pins 0-2. It is at this [Github Repo.](https://github.com/KingArthurZ3/MASA-firmware-dev) (Commit number: 2a15a8)

### Modifying the existing firmware

Most of the documentation for the exact details on how to configure each read mode should be documented in the firmware code. The README should only be for documenting project level configurations. In addition, detailed documentation

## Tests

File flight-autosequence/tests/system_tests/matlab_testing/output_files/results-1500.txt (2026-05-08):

=================================================
          FLIGHT AUTOSEQUENCE RESULTS            
=================================================

--- FLAGS ---
MECO Detected:           1
Apogee Detected:         1
  - Detection Worked:    0
  - Fallback Worked:     0
Drogue Deployed:         1
Main Deployed:           1
Landed:                  1

--- TIMESTAMPS (ms since ignition) ---
MECO Timestamp:          7510 ms
Apogee Timestamp:        26620 ms
Drogue Timestamp:        45320 ms
Main Timestamp:          92920 ms
Landed Timestamp:        92970 ms

--- KEY ALTITUDES ---
Apogee Altitude:         2440.03 m
Drogue Deploy Altitude:  1552.30 m
Main Deploy Altitude:    317.20 m

--- POST LOCKOUT KINEMATICS ---
Altitude:                0.00 m
Velocity:                0.00 m/s
Acceleration:            0.00 m/s^2

--- FALLBACK TIMER PREDICTIONS ---
Apogee time:             0 ms
Drogue deploy time:      0 ms
Main deploy time:        0 ms
Apogee altitude:         0.00 m
Drogue deploy altitude:  0.00 m
Main deploy altitude:    0.00 m
=================================================

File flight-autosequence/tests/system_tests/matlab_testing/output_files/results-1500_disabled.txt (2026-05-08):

=================================================
          FLIGHT AUTOSEQUENCE RESULTS            
=================================================

--- FLAGS ---
MECO Detected:           1
Apogee Detected:         1
  - Detection Worked:    1
  - Fallback Worked:     0
Drogue Deployed:         1
Main Deployed:           1
Landed:                  1

--- TIMESTAMPS (ms since ignition) ---
MECO Timestamp:          7510 ms
Apogee Timestamp:        34670 ms
Drogue Timestamp:        45320 ms
Main Timestamp:          91070 ms
Landed Timestamp:        91120 ms

--- KEY ALTITUDES ---
Apogee Altitude:         2155.57 m
Drogue Deploy Altitude:  1552.30 m
Main Deploy Altitude:    360.34 m

--- POST LOCKOUT KINEMATICS ---
Altitude:                2250.61 m
Velocity:                50.00 m/s
Acceleration:            -0.10 m/s^2

--- FALLBACK TIMER PREDICTIONS ---
Apogee time:             534620 ms
Drogue deploy time:      728026 ms
Main deploy time:        783444 ms
Apogee altitude:         14750.61 m
Drogue deploy altitude:  1599.00 m
Main deploy altitude:    379.80 m
=================================================

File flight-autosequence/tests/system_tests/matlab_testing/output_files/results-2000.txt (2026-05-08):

=================================================
          FLIGHT AUTOSEQUENCE RESULTS            
=================================================

--- FLAGS ---
MECO Detected:           1
Apogee Detected:         1
  - Detection Worked:    1
  - Fallback Worked:     0
Drogue Deployed:         1
Main Deployed:           1
Landed:                  1

--- TIMESTAMPS (ms since ignition) ---
MECO Timestamp:          9500 ms
Apogee Timestamp:        33060 ms
Drogue Timestamp:        78210 ms
Main Timestamp:          127010 ms
Landed Timestamp:        127060 ms

--- KEY ALTITUDES ---
Apogee Altitude:         3986.02 m
Drogue Deploy Altitude:  1550.63 m
Main Deploy Altitude:    317.26 m

--- POST LOCKOUT KINEMATICS ---
Altitude:                3965.22 m
Velocity:                20.66 m/s
Acceleration:            -9.81 m/s^2

--- FALLBACK TIMER PREDICTIONS ---
Apogee time:             33026 ms
Drogue deploy time:      68144 ms
Main deploy time:        123562 ms
Apogee altitude:         3986.99 m
Drogue deploy altitude:  1599.00 m
Main deploy altitude:    379.80 m
=================================================

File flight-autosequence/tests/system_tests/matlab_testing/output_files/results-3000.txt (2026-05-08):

=================================================
          FLIGHT AUTOSEQUENCE RESULTS            
=================================================

--- FLAGS ---
MECO Detected:           1
Apogee Detected:         1
  - Detection Worked:    1
  - Fallback Worked:     0
Drogue Deployed:         1
Main Deployed:           1
Landed:                  1

--- TIMESTAMPS (ms since ignition) ---
MECO Timestamp:          12780 ms
Apogee Timestamp:        43670 ms
Drogue Timestamp:        139120 ms
Main Timestamp:          190120 ms
Landed Timestamp:        190170 ms

--- KEY ALTITUDES ---
Apogee Altitude:         7148.22 m
Drogue Deploy Altitude:  1549.10 m
Main Deploy Altitude:    315.72 m

--- POST LOCKOUT KINEMATICS ---
Altitude:                6335.05 m
Velocity:                129.65 m/s
Acceleration:            -9.81 m/s^2

--- FALLBACK TIMER PREDICTIONS ---
Apogee time:             44140 ms
Drogue deploy time:      126390 ms
Main deploy time:        181808 ms
Apogee altitude:         7192.03 m
Drogue deploy altitude:  1599.00 m
Main deploy altitude:    379.80 m
=================================================

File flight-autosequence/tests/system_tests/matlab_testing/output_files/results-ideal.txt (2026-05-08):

=================================================
          FLIGHT AUTOSEQUENCE RESULTS            
=================================================

--- FLAGS ---
MECO Detected:           1
Apogee Detected:         1
  - Detection Worked:    1
  - Fallback Worked:     0
Drogue Deployed:         1
Main Deployed:           1
Landed:                  1

--- TIMESTAMPS (ms since ignition) ---
MECO Timestamp:          16860 ms
Apogee Timestamp:        52430 ms
Drogue Timestamp:        195430 ms
Main Timestamp:          248930 ms
Landed Timestamp:        248980 ms

--- KEY ALTITUDES ---
Apogee Altitude:         10355.65 m
Drogue Deploy Altitude:  1546.83 m
Main Deploy Altitude:    313.93 m

--- POST LOCKOUT KINEMATICS ---
Altitude:                8005.39 m
Velocity:                224.37 m/s
Acceleration:            -9.81 m/s^2

--- FALLBACK TIMER PREDICTIONS ---
Apogee time:             53799 ms
Drogue deploy time:      185755 ms
Main deploy time:        241173 ms
Apogee altitude:         10572.05 m
Drogue deploy altitude:  1599.00 m
Main deploy altitude:    379.80 m
=================================================

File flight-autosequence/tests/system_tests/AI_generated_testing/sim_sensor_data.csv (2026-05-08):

timestamp_ms | bar1_hPa | bar2_hPa | bar1_temp_C | bar2_temp_C | imu1_XL_x | imu1_XL_y | imu1_XL_z | imu1_W_x | imu1_W_y | imu1_W_z | imu2_XL_x | imu2_XL_y | imu2_XL_z | imu2_W_x | imu2_W_y | imu2_W_z
0 | 1013.229 | 1013.2196 | 15.0265 | 15.1727 | 0.0663 | 37.5436 | 0.0882 | -0.0255 | -0.0161 | -0.0346 | 0.0663 | 37.6348 | 0.0882 | -0.0255 | -0.0161 | -0.0346
20 | 1013.3312 | 1013.206 | 15.0657 | 14.9732 | 0.0591 | 37.6337 | -0.035 | 0.0498 | 0.0326 | -0.0001 | 0.0591 | 37.4137 | -0.035 | 0.0498 | 0.0326 | -0.0001
40 | 1013.1575 | 1013.1571 | 15.1113 | 14.9583 | -0.0633 | 37.3794 | 0.0331 | 0.0144 | 0.0367 | -0.046 | -0.0633 | 37.6232 | 0.0331 | 0.0144 | 0.0367 | -0.046
60 | 1013.2373 | 1013.2138 | 15.0061 | 15.0 | 0.0349 | 37.5399 | 0.0637 | 0.0302 | 0.0137 | 0.0148 | 0.0349 | 37.4843 | 0.0637 | 0.0302 | 0.0137 | 0.0148
80 | 1013.2207 | 1013.1491 | 15.1035 | 14.9344 | 0.1209 | 37.5498 | 0.0121 | -0.0158 | -0.0025 | -0.0014 | 0.1209 | 37.4935 | 0.0121 | -0.0158 | -0.0025 | -0.0014
100 | 1013.2497 | 1013.1936 | 14.8636 | 15.1413 | 0.064 | 37.4608 | 0.0486 | -0.0245 | 0.0106 | 0.0247 | 0.064 | 37.5959 | 0.0486 | -0.0245 | 0.0106 | 0.0247
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

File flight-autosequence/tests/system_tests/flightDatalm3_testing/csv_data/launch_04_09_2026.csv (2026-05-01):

time (ms) | deltaTime (ms) | status | baro-altitude (m) | dedrck-v-speed (m/s) | angle (deg) | roll-rate (deg/s) | vert-accel (m/s2) | accel (m/s2) | dedrck-alti (m) | baro-speed (m/s) | amb-temp (deg c) | batt-voltage (mV) | P1-state | P2-state | P3-state | analog1 (mV) | analog2 (mV) | inFreefall | gpsLat | gpsLng | gpsAltMSL | gpsState | gpsSats
4203 | 20 | 3 | 0 | 0 | 4,1 | 0 | 0,0 | 9,9 | 0 | 0,0 | 30 | 6174 | 0 | 0 | 0 | 4 | 2 | 0 | 41,777897 | -86,576866 | 187 | 1 | 10
4223 | 20 | 3 | 0 | 0 | 3,2 | 0 | 0,0 | 9,7 | 0 | 0,0 | 30 | 6164 | 0 | 0 | 0 | 4 | 1 | 0 | 41,777897 | -86,576866 | 187 | 1 | 10
4243 | 20 | 3 | 0 | 0 | 3,2 | 0 | 0,0 | 9,7 | 0 | 0,0 | 30 | 6162 | 0 | 0 | 0 | 4 | 2 | 0 | 41,777897 | -86,576866 | 187 | 1 | 10
4263 | 20 | 3 | 0 | 0 | 4,6 | 0 | 0,0 | 9,7 | 0 | 0,0 | 30 | 6159 | 0 | 0 | 0 | 5 | 3 | 0 | 41,777897 | -86,576866 | 187 | 1 | 10
4283 | 20 | 3 | 0 | 0 | 4,6 | 0 | 0,0 | 9,7 | 0 | 0,0 | 30 | 6157 | 0 | 0 | 0 | 3 | 3 | 0 | 41,777897 | -86,576866 | 187 | 1 | 10
4303 | 20 | 3 | 0 | 0 | 4,8 | 0 | 0,0 | 9,6 | 0 | 0,0 | 30 | 6159 | 0 | 0 | 0 | 4 | 2 | 0 | 41,777897 | -86,576866 | 187 | 1 | 10
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

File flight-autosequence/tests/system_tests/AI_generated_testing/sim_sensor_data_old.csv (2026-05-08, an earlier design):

timestamp_ms | bar1_hPa | bar2_hPa | bar1_temp_C | bar2_temp_C | imu1_XL_x | imu1_XL_y | imu1_XL_z | imu1_W_x | imu1_W_y | imu1_W_z | imu2_XL_x | imu2_XL_y | imu2_XL_z | imu2_W_x | imu2_W_y | imu2_W_z
0 | 1013.2414 | 1013.2407 | 19.9889 | 20.1062 | 0.0 | 9.7875 | 0.0 | 0.0 | 0.0 | 0.0 | 0.0 | 9.5596 | 0.0 | 0.0 | 0.0 | 0.0
20 | 1013.2699 | 1013.2356 | 19.9783 | 20.0593 | 0.0 | 9.8415 | 0.0 | 0.0 | 0.0 | 0.0 | 0.0 | 9.9986 | 0.0 | 0.0 | 0.0 | 0.0
40 | 1013.2894 | 1013.256 | 19.9262 | 19.9688 | 0.0 | 9.8436 | 0.0 | 0.0 | 0.0 | 0.0 | 0.0 | 10.023 | 0.0 | 0.0 | 0.0 | 0.0
60 | 1013.2525 | 1013.2443 | 20.0532 | 19.9337 | 0.0 | 9.7598 | 0.0 | 0.0 | 0.0 | 0.0 | 0.0 | 9.8876 | 0.0 | 0.0 | 0.0 | 0.0
80 | 1013.3024 | 1013.237 | 20.0377 | 20.0699 | 0.0 | 9.924 | 0.0 | 0.0 | 0.0 | 0.0 | 0.0 | 9.623 | 0.0 | 0.0 | 0.0 | 0.0
100 | 1013.2841 | 1013.1682 | 19.738 | 20.0014 | 0.0 | 9.6693 | 0.0 | 0.0 | 0.0 | 0.0 | 0.0 | 9.9512 | 0.0 | 0.0 | 0.0 | 0.0
120 | 1013.2899 | 1013.1842 | 20.0847 | 19.9698 | 0.0 | 9.7937 | 0.0 | 0.0 | 0.0 | 0.0 | 0.0 | 9.7582 | 0.0 | 0.0 | 0.0 | 0.0
140 | 1013.2569 | 1013.2942 | 20.0638 | 20.078 | 0.0 | 9.9041 | 0.0 | 0.0 | 0.0 | 0.0 | 0.0 | 9.8856 | 0.0 | 0.0 | 0.0 | 0.0
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

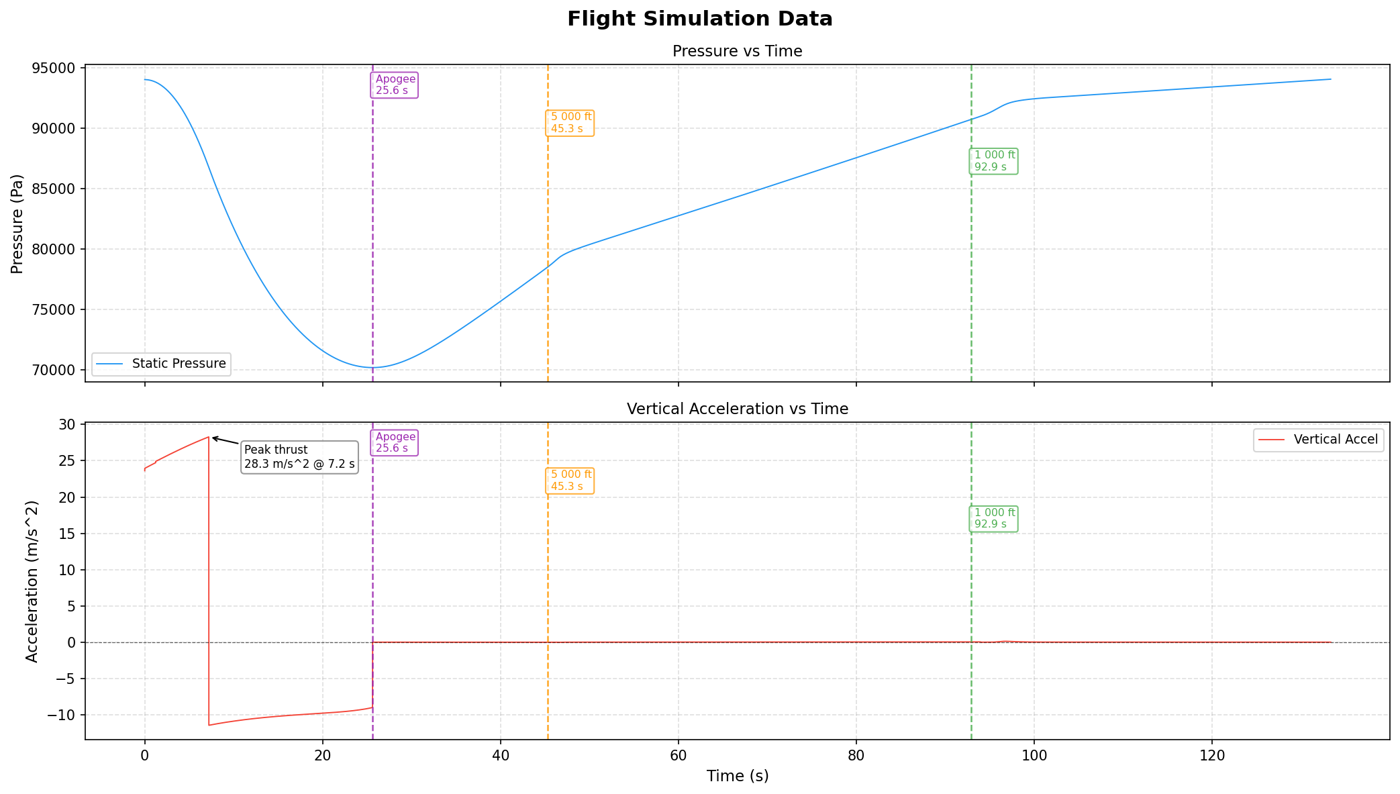
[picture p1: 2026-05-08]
flight-autosequence/tests/system_tests/matlab_testing/graphs/flight_plots-1500.png

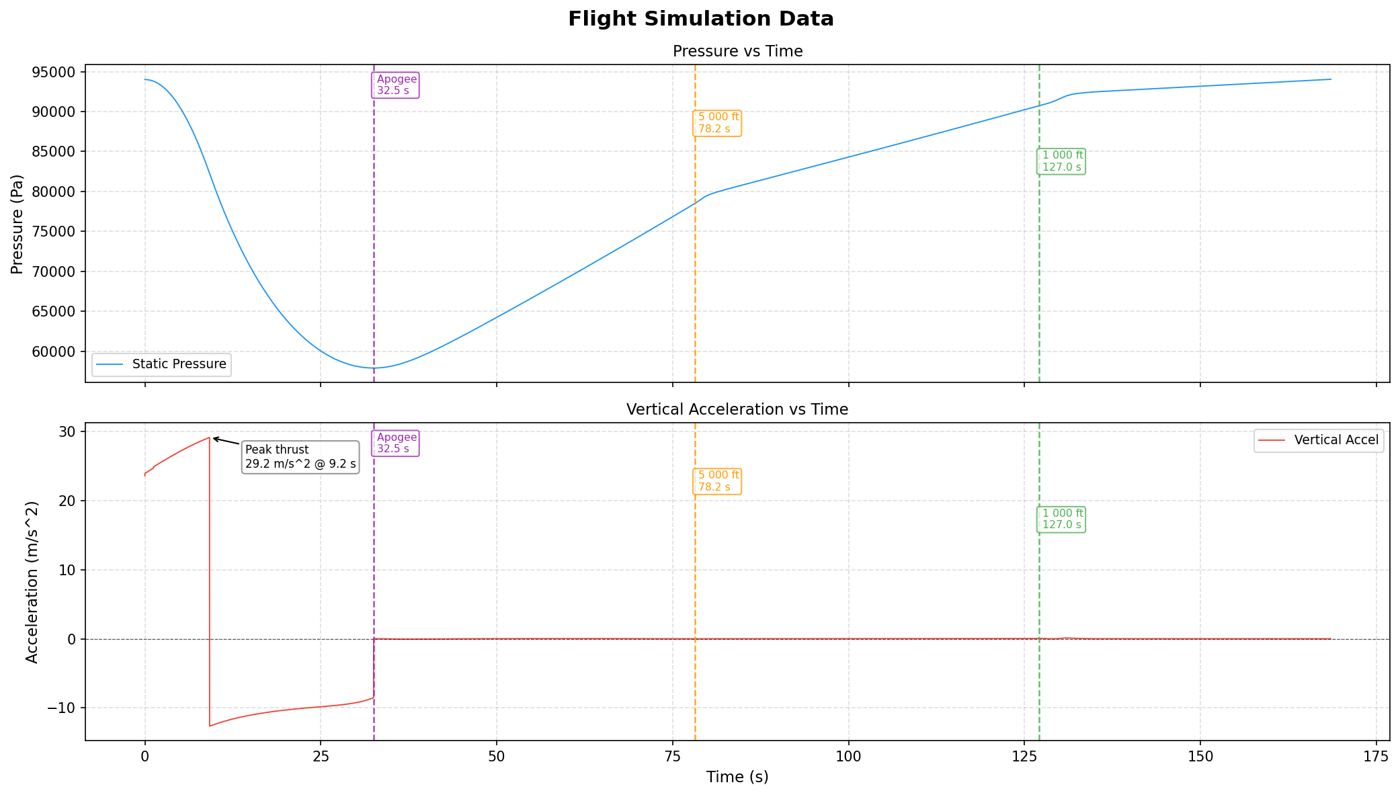
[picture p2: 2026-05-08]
flight-autosequence/tests/system_tests/matlab_testing/graphs/flight_plots-2000.png

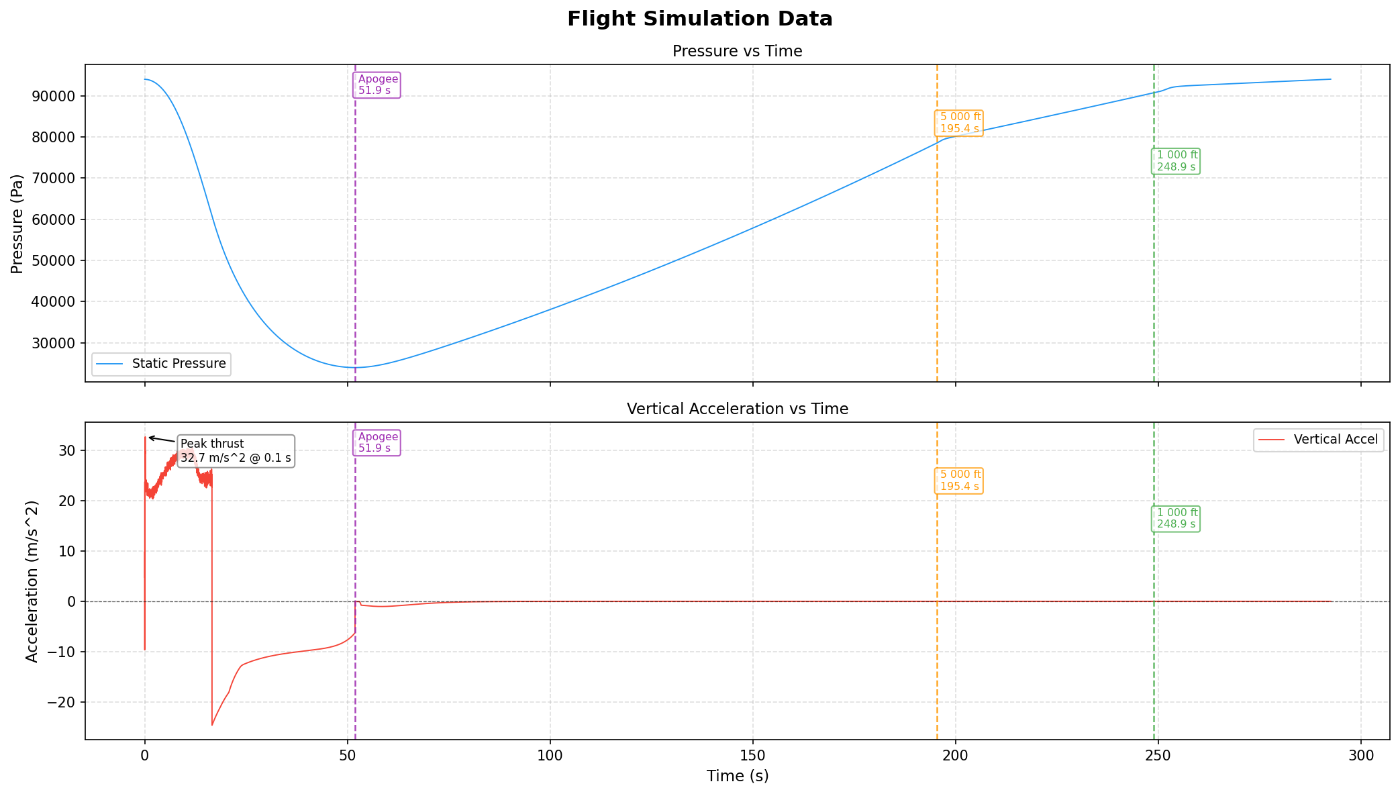
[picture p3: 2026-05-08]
flight-autosequence/tests/system_tests/matlab_testing/graphs/flight_plots-ideal.png

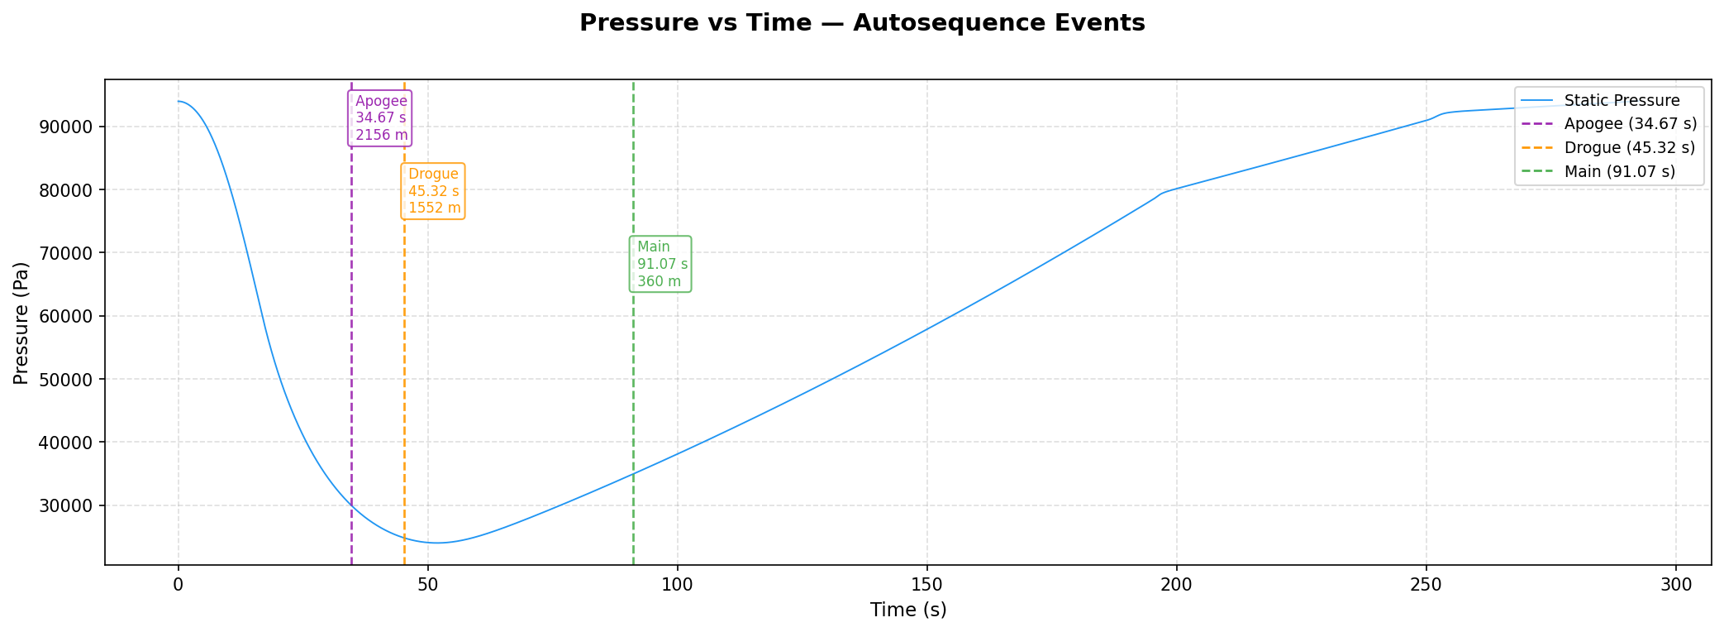
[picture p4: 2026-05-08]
flight-autosequence/tests/system_tests/matlab_testing/graphs/pressure_results-ideal.png

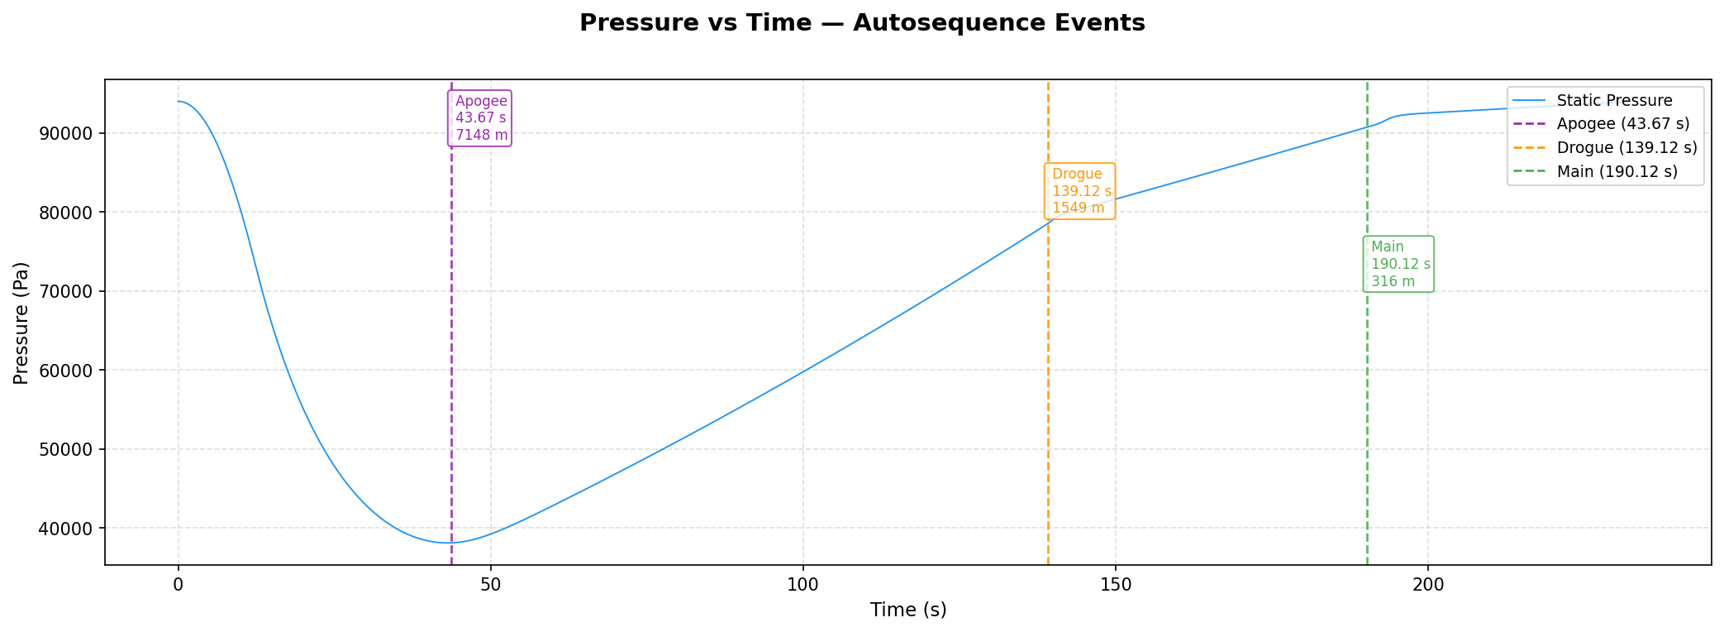
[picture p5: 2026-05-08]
flight-autosequence/tests/system_tests/matlab_testing/graphs/pressure_results-3000.png

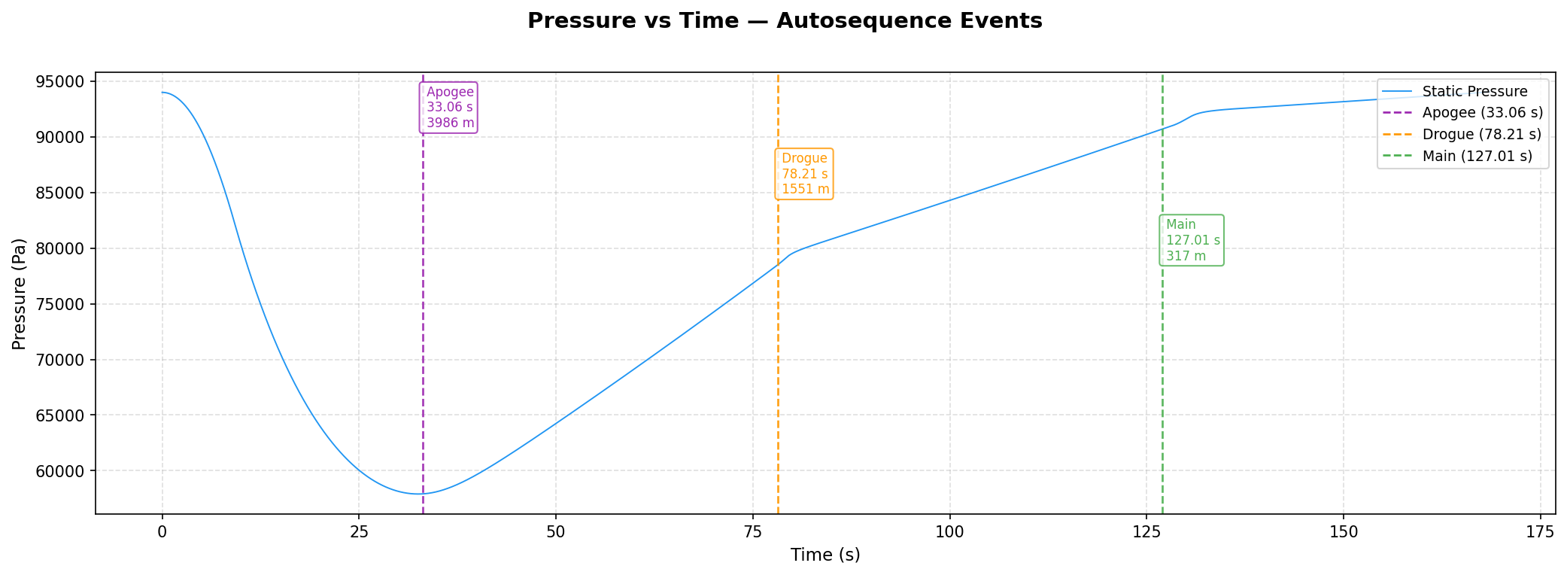
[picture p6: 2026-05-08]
flight-autosequence/tests/system_tests/matlab_testing/graphs/pressure_results-2000.png

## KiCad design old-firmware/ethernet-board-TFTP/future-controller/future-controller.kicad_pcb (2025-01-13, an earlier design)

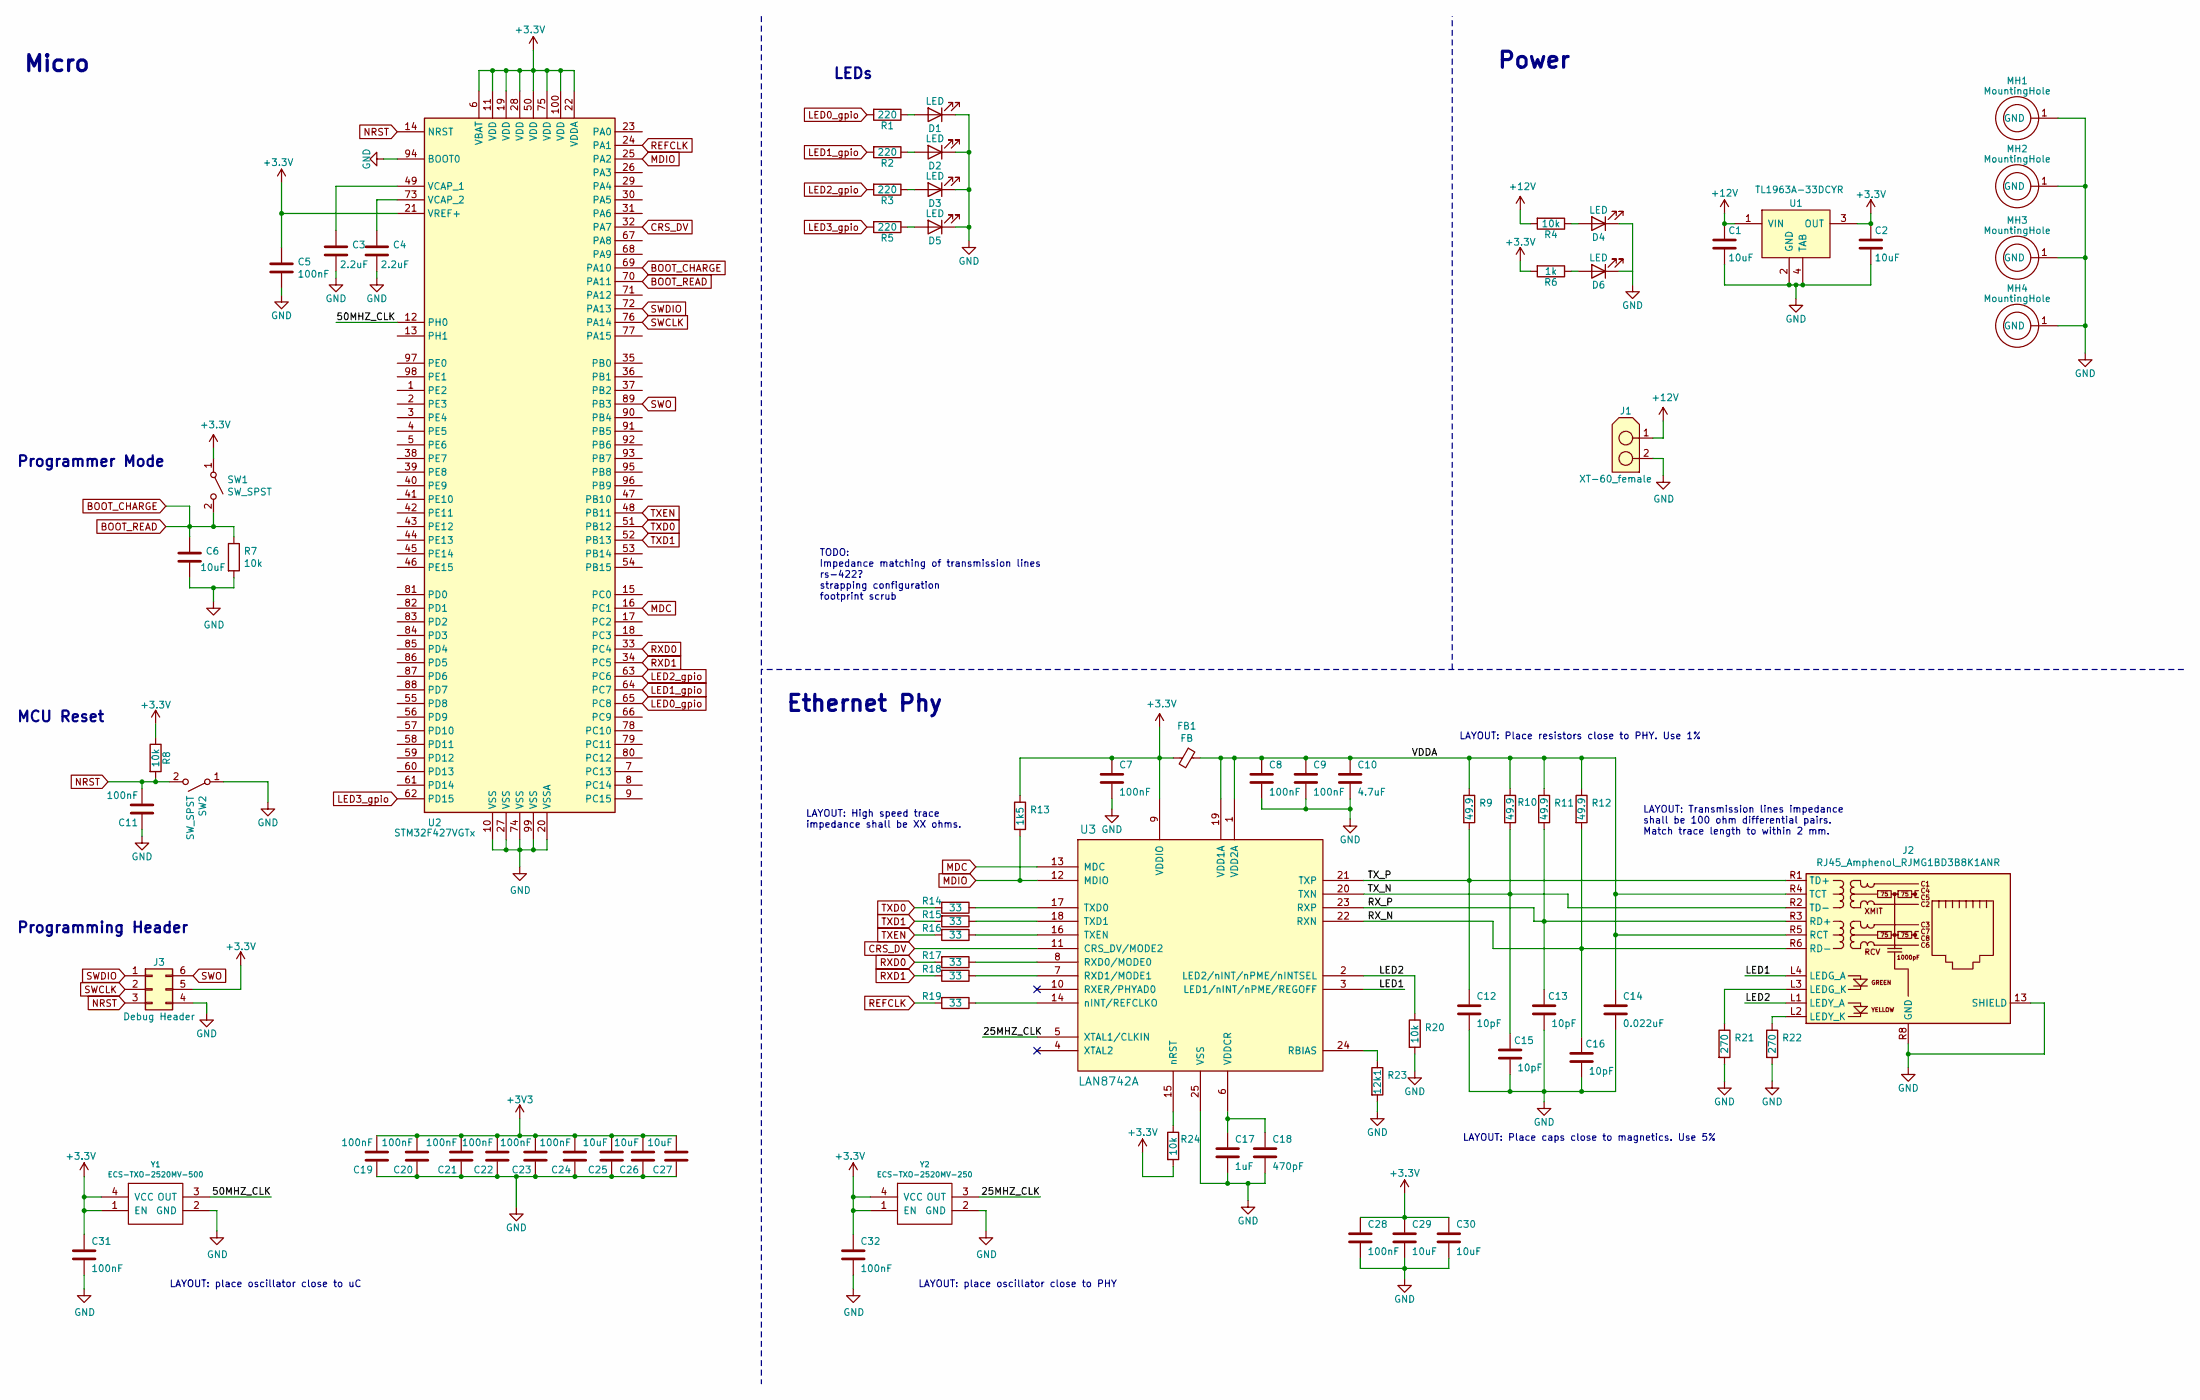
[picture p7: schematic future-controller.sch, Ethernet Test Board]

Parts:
C1, C2: 10uF; C_1206_3216Metric
C3, C4: 2.2uF; C_0603_1608Metric
C5, C7, C8, C9, C11, C19, C20, C21, C22, C23, C24, C28, C31, C32: 100nF; C_0603_1608Metric
C6, C25, C26, C27, C29, C30: 10uF; C_0603_1608Metric
C10: 4.7uF; C_0603_1608Metric
C12, C13, C15, C16: 10pF; C_0402_1005Metric
C14: 0.022uF; C_0603_1608Metric
C17: 1uF; C_0603_1608Metric
C18: 470pF; C_0603_1608Metric
D1, D2, D3, D4, D5, D6: LED; LED_0603_1608Metric
FB1: FB; C_0603_1608Metric
J1: XT-60_female; XT-60
J2: RJ45_Amphenol_RJMG1BD3B8K1ANR; RJ45_Amphenol_RJMG1BD3B8K1ANR_modified
J3: Debug Header; PinHeader_2x03_P2.54mm_Vertical
MH1, MH2, MH3, MH4: MountingHole; MountingHole_3.2mm_M3_Pad
R1, R2, R3, R5: 220; R_0603_1608Metric
R4, R7, R8, R20, R24: 10k; R_0603_1608Metric
R6: 1k; R_0603_1608Metric
R9, R10, R11, R12: 49.9; R_0603_1608Metric
R13: 1k5; R_0603_1608Metric
R14, R15, R16, R17, R18, R19: 33; R_0603_1608Metric
R21, R22: 270; R_0603_1608Metric
R23: 12k1; R_0603_1608Metric
SW1, SW2: SW_SPST; SKQGADE010
U1: TL1963A-33DCYR; SOT-223
U2: STM32F427VGTx; LQFP-100_14x14mm_P0.5mm
U3: LAN8742A; QFN-24-1EP_4x4mm_P0.5mm_EP2.6x2.6mm
Y1: ECS-TXO-2520MV-500; Oscillator_SMD_Kyocera_KC2520Z-4Pin_2.5x2.0mm
Y2: ECS-TXO-2520MV-250; Oscillator_SMD_Kyocera_KC2520Z-4Pin_2.5x2.0mm

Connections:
+12V: C1.1, J1.1, R4.2, U1.1 (VIN)
/25MHZ_CLK: U3.5 (XTAL1/CLKIN), Y2.3 (OUT)
/50MHZ_CLK: U2.12 (PH0), Y1.3 (OUT)
/LED1: J2.L4 (LEDG_A), U3.3 (LED1/nINT/nPME/REGOFF)
/LED2: J2.L1 (LEDY_A), R20.1, U3.2 (LED2/nINT/nPME/nINTSEL)
/RX_N: C16.1, J2.R6 (RD-), R12.2, U3.22 (RXN)
/RX_P: C13.1, J2.R3 (RD+), R11.2, U3.23 (RXP)
/TX_N: C15.1, J2.R2 (TD-), R10.2, U3.20 (TXN)
/TX_P: C12.1, J2.R1 (TD+), R9.2, U3.21 (TXP)
/VDDA: C8.1, C9.1, C10.1, C14.1, FB1.1, J2.R4 (TCT), J2.R5 (RCT), R9.1, R10.1, R11.1, R12.1, U3.1 (VDD2A), U3.19 (VDD1A)
BOOT_CHARGE: C6.1, R7.1, SW1.2 (B), U2.69 (PA10), U2.70 (PA11); also elsewhere on the board
CRS_DV: U2.32 (PA7), U3.11 (CRS_DV/MODE2)
GND: C1.2, C2.2, C3.2, C4.2, C5.2, C6.2, C7.2, C8.2, C9.2, C10.2, C11.1, C12.2, C13.2, C14.2, C15.2, C16.2, C17.2, C18.2, C19.1, C20.1, C21.1, C22.1, C23.1, C24.1, C25.1, C26.1, C27.1, C28.2, C29.2, C30.2, C31.2, C32.2, D1.1 (K), D2.1 (K), D3.1 (K), D4.1 (K), D5.1 (K), D6.1 (K), J1.2, J2.13 (SHIELD), J2.R8 (GND), J3.4, MH1.1, MH2.1, MH3.1, MH4.1, R7.2, R20.2, R21.2, R22.2, R23.2, SW2.1 (A), U1.2 (GND), U1.4 (TAB), U2.10 (VSS), U2.20 (VSSA), U2.27 (VSS), U2.74 (VSS), U2.94 (BOOT0), U2.99 (VSS), U3.25 (VSS), Y1.2 (GND), Y2.2 (GND); also elsewhere on the board
LED0_gpio: R1.2, U2.65 (PC8)
LED1_gpio: R2.2, U2.64 (PC7)
LED2_gpio: R3.2, U2.63 (PC6)
LED3_gpio: R5.2, U2.62 (PD15)
MDC: U2.16 (PC1), U3.13 (MDC)
MDIO: R13.2, U2.25 (PA2), U3.12 (MDIO)
NRST: C11.2, J3.3, R8.2, SW2.2 (B), U2.14 (NRST); also elsewhere on the board
unnamed: C3.1, U2.49 (VCAP_1)
unnamed: C4.1, U2.73 (VCAP_2)
unnamed: C17.1, C18.1, U3.6 (VDDCR)
unnamed: D1.2 (A), R1.1
unnamed: D2.2 (A), R2.1
unnamed: D3.2 (A), R3.1
unnamed: D4.2 (A), R4.1
unnamed: D5.2 (A), R5.1
unnamed: D6.2 (A), R6.1
unnamed: J2.L2 (LEDY_K), R22.1
unnamed: J2.L3 (LEDG_K), R21.1
unnamed: R14.1, U3.17 (TXD0)
unnamed: R15.1, U3.18 (TXD1)
unnamed: R16.1, U3.16 (TXEN)
unnamed: R17.1, U3.8 (RXD0/MODE0)
unnamed: R18.1, U3.7 (RXD1/MODE1)
unnamed: R19.1, U3.14 (nINT/REFCLKO)
unnamed: R23.1, U3.24 (RBIAS)
unnamed: R24.1, U3.15 (nRST)
REFCLK: R19.2, U2.24 (PA1)
RXD0: R17.2, U2.33 (PC4)
RXD1: R18.2, U2.34 (PC5)
SWCLK: J3.2, U2.76 (PA14)
SWDIO: J3.1, U2.72 (PA13)
SWO: J3.6, U2.89 (PB3)
TXD0: R14.2, U2.51 (PB12)
TXD1: R15.2, U2.52 (PB13)
TXEN: R16.2, U2.48 (PB11)

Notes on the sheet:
Power
Programming Header
MCU Reset
LEDs
Programmer Mode
Ethernet Phy
LAYOUT: Transmission lines impedance shall be 100 ohm differential pairs. Match trace length to within 2 mm.
LAYOUT: High speed trace impedance shall be XX ohms.
TODO: Impedance matching of transmission lines rs-422? strapping configuration footprint scrub
LAYOUT: place oscillator close to PHY
Micro
LAYOUT: place oscillator close to uC
LAYOUT: Place caps close to magnetics. Use 5%
LAYOUT: Place resistors close to PHY. Use 1%

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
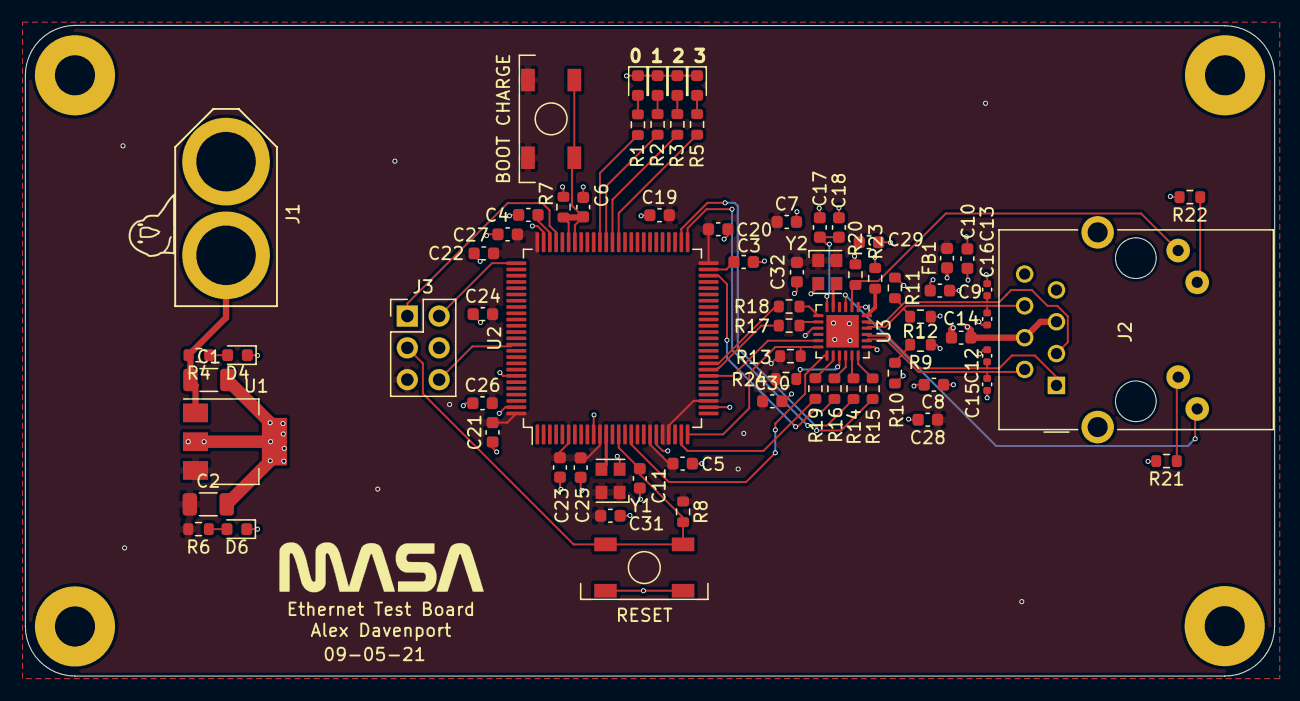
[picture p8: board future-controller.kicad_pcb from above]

Board: 4 copper layers, 99.8 x 52.0 mm, 77 parts (0 on the bottom side), 49 nets.

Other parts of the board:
BOOT CHARGE: SW_SPST; SKQGADE010
RESET: SW_SPST; SKQGADE010

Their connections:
BOOT_CHARGE: BOOT CHARGE.2; also elsewhere on the board
GND: RESET.1; also elsewhere on the board
NRST: RESET.2; also elsewhere on the board

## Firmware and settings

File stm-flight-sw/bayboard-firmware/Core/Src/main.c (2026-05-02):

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
/* Includes ------------------------------------------------------------------*/
#include "main.h"
#include "cmsis_os.h"
#include "lwip.h"

/* USER CODE BEGIN Includes */
#include "MS5611.h"
#include "ADS1120.h"
#include "MAX11128.h"
#include "LSM6DSO32XTR.h"
#include "VLVs.h"
#include "api.h"
#include "string.h"
#include "client.h"
#include "messages.h"
#include "M24256E.h"
#include "utils.h"
#include "lmp_channels.h"
#include "lwip/udp.h"
#include "log_errors.h"
#include "queue.h"
#include "eeprom-config.h"
#include "telemetry.h"
#include "network-processing.h"
#include "board-state.h"
#include "logging.h"
#include "time-sync.h"
#include "udptelemetry.h"
//#include "lwip/netif.h"
/* USER CODE END Includes */

/* USER CODE BEGIN PM */
void __malloc_lock(struct _reent *r) {
    if(xTaskGetSchedulerState() != taskSCHEDULER_NOT_STARTED) {
        vTaskSuspendAll();
    }
}

void __malloc_unlock(struct _reent *r) {
    if(xTaskGetSchedulerState() != taskSCHEDULER_NOT_STARTED) {
        (void)xTaskResumeAll();
    }
}
/* USER CODE END PM */


CRC_HandleTypeDef hcrc;

I2C_HandleTypeDef hi2c1;
I2C_HandleTypeDef hi2c5;

RTC_HandleTypeDef hrtc;

SPI_HandleTypeDef hspi1;
SPI_HandleTypeDef hspi2;
SPI_HandleTypeDef hspi4;
SPI_HandleTypeDef hspi6;

/* Definitions for startTask */
osThreadId_t startTaskHandle;
const osThreadAttr_t startTask_attributes = {
  .name = "startTask",
  .stack_size = 1024 * 4,
  .priority = (osPriority_t) osPriorityNormal,
};
/* USER CODE BEGIN PV */
extern struct netif gnetif;

ip4_addr_t bb_addr;
uint8_t bb_num;

inittimers_t timers = {0};
SemaphoreHandle_t timer_mutex = NULL;

EEPROM_conf_t loaded_config = {0};
PT_t PT1_h = {0.5f, 5000.0f, 4.5f}; // Default
PT_t PT2_h = {0.5f, 5000.0f, 4.5f};
PT_t PT3_h = {0.5f, 5000.0f, 4.5f};
PT_t PT4_h = {0.5f, 5000.0f, 4.5f};
PT_t PT5_h = {0.5f, 5000.0f, 4.5f};
PT_t PT6_h = {0.5f, 5000.0f, 4.5f};
PT_t PT7_h = {0.5f, 5000.0f, 4.5f};
PT_t PT8_h = {0.5f, 5000.0f, 4.5f};
PT_t PT9_h = {0.5f, 5000.0f, 4.5f};
PT_t PT10_h = {0.5f, 5000.0f, 4.5f};

Sensors_t sensors_h = {0};

osThreadId_t telemetryTaskHandle;
const osThreadAttr_t telemetry_task_attr = {
  .name = "telemetryTask",
  .stack_size = 512 * 4,
  .priority = (osPriority_t) osPriorityNormal,
};

osThreadId_t telemetrySendTaskHandle;
const osThreadAttr_t telemetry_send_task_attr = {
  .name = "telemSendTask",
  .stack_size = 512 * 4,
  .priority = (osPriority_t) osPriorityNormal,
};

osThreadId_t packetTaskHandle;
const osThreadAttr_t packet_task_attr = {
  .name = "packetTask",
  .stack_size = 512 * 4,
  .priority = (osPriority_t) osPriorityNormal,
};

osThreadId_t flashClearTaskHandle;
const osThreadAttr_t flash_clear_task_attr = {
  .name = "flashCTask",
  .stack_size = 1024 * 4,
  .priority = (osPriority_t) osPriorityNormal,
};
/* USER CODE END PV */

void SystemClock_Config(void);
static void MPU_Config(void);
static void MX_GPIO_Init(void);
static void MX_RTC_Init(void);
static void MX_CRC_Init(void);
static void MX_I2C1_Init(void);
static void MX_I2C5_Init(void);
static void MX_SPI1_Init(void);
static void MX_SPI2_Init(void);
static void MX_SPI4_Init(void);
static void MX_SPI6_Init(void);
void StartAndMonitor(void *argument);

/* USER CODE BEGIN 0 */
uint64_t getTimestamp() {
	return HAL_GetTick();
}

void toggleBuzzer(TimerHandle_t xTimer) {
	HAL_GPIO_TogglePin(BUZZ_GPIO_Port, BUZZ_Pin);
}

void toggleLEDPins(TimerHandle_t xTimer) {
	HAL_GPIO_TogglePin(LED_RED_GPIO_Port, LED_RED_Pin);
	HAL_GPIO_TogglePin(LED_GREEN_GPIO_Port, LED_GREEN_Pin);
	HAL_GPIO_TogglePin(LED_BLUE_GPIO_Port, LED_BLUE_Pin);
}

void buzzerOff() {
	HAL_GPIO_WritePin(BUZZ_GPIO_Port, BUZZ_Pin, 0);
}

void buzzerOn() {
	HAL_GPIO_WritePin(BUZZ_GPIO_Port, BUZZ_Pin, 1);
}

void stopLEDtimer() {
	if(xSemaphoreTake(timer_mutex, 1) == pdPASS) {
		if(timers.ledTimer) {
			xTimerStop(timers.ledTimer, 0);
			HAL_GPIO_WritePin(LED_RED_GPIO_Port, LED_RED_Pin, 1);
			HAL_GPIO_WritePin(LED_GREEN_GPIO_Port, LED_GREEN_Pin, 1);
			HAL_GPIO_WritePin(LED_BLUE_GPIO_Port, LED_BLUE_Pin, 1);
		}
		xSemaphoreGive(timer_mutex);
	}
}

void start_led_timer(TickType_t delay, uint32_t reload, uint8_t force) {
	if(xSemaphoreTake(timer_mutex, 0) == pdPASS) {
		if(timers.ledTimer) {
			if(force || xTimerIsTimerActive(timers.ledTimer) != pdPASS) {
				vTimerSetTimerID(timers.ledTimer, (void *)reload);
				xTimerChangePeriod(timers.ledTimer, delay, 0);
			}
		}
		xSemaphoreGive(timer_mutex);
	}
}

void start_buzz_timer(TickType_t delay, uint32_t reload, uint8_t force, uint8_t startMode) {
	if(xSemaphoreTake(timer_mutex, 0) == pdPASS) {
		if(timers.buzzTimer) {
			if(force || xTimerIsTimerActive(timers.buzzTimer) != pdPASS) {
				HAL_GPIO_WritePin(BUZZ_GPIO_Port, BUZZ_Pin, startMode);
				vTimerSetTimerID(timers.buzzTimer, (void *)reload);
				xTimerChangePeriod(timers.buzzTimer, delay, 0);
			}
		}
		xSemaphoreGive(timer_mutex);
	}
}

void BuzzTimer(TimerHandle_t xTimer) {
    uint32_t toggleCount = (uint32_t) pvTimerGetTimerID(xTimer);

    HAL_GPIO_TogglePin(BUZZ_GPIO_Port, BUZZ_Pin);

    if(toggleCount == 0) {
    	HAL_GPIO_WritePin(BUZZ_GPIO_Port, BUZZ_Pin, 0);
        xTimerStop(xTimer, 0);
        return;
    }

    toggleCount--;

    vTimerSetTimerID(xTimer, (void *)toggleCount);
}

void LEDTimer(TimerHandle_t xTimer) {
    uint32_t toggleCount = (uint32_t) pvTimerGetTimerID(xTimer);

	HAL_GPIO_TogglePin(LED_RED_GPIO_Port, LED_RED_Pin);
	HAL_GPIO_TogglePin(LED_GREEN_GPIO_Port, LED_GREEN_Pin);
	HAL_GPIO_TogglePin(LED_BLUE_GPIO_Port, LED_BLUE_Pin);

    if(toggleCount == 0) {
		HAL_GPIO_WritePin(LED_RED_GPIO_Port, LED_RED_Pin, 1);
		HAL_GPIO_WritePin(LED_GREEN_GPIO_Port, LED_GREEN_Pin, 1);
		HAL_GPIO_WritePin(LED_BLUE_GPIO_Port, LED_BLUE_Pin, 1);
        xTimerStop(xTimer, 0);
        return;
    }

    toggleCount--;

    vTimerSetTimerID(xTimer, (void *)toggleCount);
}

static void Enable_GPIO_Clock(GPIO_TypeDef *port) {
    if (port == GPIOA) __HAL_RCC_GPIOA_CLK_ENABLE();
    else if (port == GPIOB) __HAL_RCC_GPIOB_CLK_ENABLE();
    else if (port == GPIOC) __HAL_RCC_GPIOC_CLK_ENABLE();
    else if (port == GPIOD) __HAL_RCC_GPIOD_CLK_ENABLE();
    else if (port == GPIOE) __HAL_RCC_GPIOE_CLK_ENABLE();
    else if (port == GPIOF) __HAL_RCC_GPIOF_CLK_ENABLE();
    else if (port == GPIOG) __HAL_RCC_GPIOG_CLK_ENABLE();
    else if (port == GPIOH) __HAL_RCC_GPIOH_CLK_ENABLE();
#ifdef GPIOI
    else if (port == GPIOI) __HAL_RCC_GPIOI_CLK_ENABLE();
#endif
    else if (port == GPIOJ) __HAL_RCC_GPIOJ_CLK_ENABLE();
    else if (port == GPIOK) __HAL_RCC_GPIOK_CLK_ENABLE();
}

void clear_i2c_bus(GPIO_TypeDef * scl_port, uint16_t scl_pin, GPIO_TypeDef * sda_port, uint16_t sda_pin) {
	Enable_GPIO_Clock(scl_port);
	Enable_GPIO_Clock(sda_port);

    GPIO_InitTypeDef GPIO_InitStruct = {0};

    GPIO_InitStruct.Pin = scl_pin;
    GPIO_InitStruct.Mode = GPIO_MODE_OUTPUT_OD;
    GPIO_InitStruct.Pull = GPIO_NOPULL;
    GPIO_InitStruct.Speed = GPIO_SPEED_FREQ_HIGH;
    HAL_GPIO_Init(scl_port, &GPIO_InitStruct);

    GPIO_InitStruct.Pin = sda_pin;
    GPIO_InitStruct.Mode = GPIO_MODE_OUTPUT_OD;
    GPIO_InitStruct.Pull = GPIO_NOPULL;
    GPIO_InitStruct.Speed = GPIO_SPEED_FREQ_HIGH;
    HAL_GPIO_Init(sda_port, &GPIO_InitStruct);

    HAL_GPIO_WritePin(sda_port, sda_pin, GPIO_PIN_SET);

    for (uint8_t i = 0; i < 9; i++) {
        if (HAL_GPIO_ReadPin(sda_port, sda_pin) == GPIO_PIN_SET) {
            break;
        }

        HAL_GPIO_WritePin(scl_port, scl_pin, GPIO_PIN_RESET);
        HAL_Delay(1);

        HAL_GPIO_WritePin(scl_port, scl_pin, GPIO_PIN_SET);
        HAL_Delay(1);
    }

    HAL_GPIO_WritePin(scl_port, scl_pin, GPIO_PIN_SET);
    HAL_Delay(1);
    HAL_GPIO_WritePin(sda_port, sda_pin, GPIO_PIN_RESET);
    HAL_Delay(1);
    HAL_GPIO_WritePin(sda_port, sda_pin, GPIO_PIN_SET);
    HAL_Delay(1);

    HAL_GPIO_DeInit(sda_port, sda_pin);
    HAL_GPIO_DeInit(scl_port, scl_pin);
}
/* USER CODE END 0 */

/**
  * @brief  The application entry point.
  * @retval int
  */
int main(void)
{

  /* MPU Configuration--------------------------------------------------------*/
  MPU_Config();

  /* Enable the CPU Cache */

  /* Enable I-Cache---------------------------------------------------------*/
  SCB_EnableICache();

  /* Enable D-Cache---------------------------------------------------------*/
  SCB_EnableDCache();

  /* MCU Configuration--------------------------------------------------------*/

  /* Reset of all peripherals, Initializes the Flash interface and the Systick. */
  HAL_Init();

  /* Configure the system clock */
  SystemClock_Config();

  /* USER CODE BEGIN SysInit */
  // RTC init code - enable backup domain access because we're using HSE / 60 as RTC clock source
  HAL_PWR_EnableBkUpAccess();
  // Force reset RTC registers in case something got corrupted
  __HAL_RCC_BACKUPRESET_FORCE();
  __HAL_RCC_BACKUPRESET_RELEASE();

  clear_i2c_bus(GPIOB, GPIO_PIN_6, GPIOB, GPIO_PIN_7);
  clear_i2c_bus(GPIOA, GPIO_PIN_8, GPIOC, GPIO_PIN_9);
  /* USER CODE END SysInit */

  /* Initialize all configured peripherals */
  MX_GPIO_Init();
  MX_RTC_Init();
  MX_CRC_Init();
  MX_I2C1_Init();
  MX_I2C5_Init();
  MX_SPI1_Init();
  MX_SPI2_Init();
  MX_SPI4_Init();
  MX_SPI6_Init();
  /* Init scheduler */
  osKernelInitialize();

  /* USER CODE BEGIN RTOS_MUTEX */
  /* add mutexes, ... */
  timer_mutex = xSemaphoreCreateMutex();
  timers.buzzTimer = xTimerCreate("buzz", 1000, pdTRUE, (void *)0, BuzzTimer);
  timers.ledTimer = xTimerCreate("led", 1000, pdTRUE, (void *)0, LEDTimer);
  timesync_setup(&hrtc);
  if(logging_setup()) {
	  for(;;) {}
  }
  if(telemetry_setup()) {
	  for(;;) {}
  }
  /* USER CODE END RTOS_MUTEX */

  /* USER CODE BEGIN RTOS_SEMAPHORES */
  /* add semaphores, ... */
  /* USER CODE END RTOS_SEMAPHORES */

  /* USER CODE BEGIN RTOS_TIMERS */
  /* start timers, add new ones, ... */
  /* USER CODE END RTOS_TIMERS */

  /* USER CODE BEGIN RTOS_QUEUES */
  /* add queues, ... */

  // This next section is considered the "critical" portion of initialization. This portion has no access to logging and therefore needs to communicate status other ways. The section ends on the return of the MX_LWIP_Init function
  // The end of this section is marked by a UDP message and/or the on-board LED becoming solid and/or a short buzzer beep

  // Load EEPROM config
  loaded_config.pt1 = &PT1_h;
  loaded_config.pt2 = &PT2_h;
  loaded_config.pt3 = &PT3_h;
  loaded_config.pt4 = &PT4_h;
  loaded_config.pt5 = &PT5_h;
  loaded_config.pt6 = &PT6_h;
  loaded_config.pt7 = &PT7_h;
  loaded_config.pt8 = &PT8_h;
  loaded_config.pt9 = &PT9_h;
  loaded_config.pt10 = &PT10_h;
  if(setup_eeprom(&hi2c1, EEPROM_WC_GPIO_Port, EEPROM_WC_Pin)) {
#ifdef EEPROM_OVERRIDE
	  load_eeprom_defaults(&loaded_config, &bb_num);
	  log_message(STAT_EEPROM_DEFAULT_LOADED, -1);
#else
	  switch(load_eeprom_config(&loaded_config, &bb_num)) {
	  	  case -1: {
	  		  // eeprom load error, defaults loaded
	  		  load_eeprom_defaults(&loaded_config, &bb_num);
	  		  log_message(ERR_EEPROM_LOAD_COMM_ERR, -1);
	  		  start_buzz_timer(500, UINT32_MAX, 1, 0);
	  		  break;
	  	  }
	  	  case -2: {
	  		  // eeprom tc gain value error
	  		  load_eeprom_defaults(&loaded_config, &bb_num);
	  		  log_message(ERR_EEPROM_LOAD_TC_ERR, -1);
	  		  start_buzz_timer(500, UINT32_MAX, 1, 0);
	  		  break;
	  	  }
	  	  case -3: {
	  		  // eeprom valve conf error
	  		  load_eeprom_defaults(&loaded_config, &bb_num);
	  		  log_message(ERR_EEPROM_LOAD_VLV_ERR, -1);
	  		  start_buzz_timer(500, UINT32_MAX, 1, 0);
	  		  break;
	  	  }
	  	  case -4: {
	  		  // invalid bb number
	  		  load_eeprom_defaults(&loaded_config, &bb_num);
	  		  log_message(BB_ERR_EEPROM_LOAD_BB_NUM_ERR, -1);
	  		  start_buzz_timer(500, UINT32_MAX, 1, 0);
	  		  break;
	  	  }
	  	  default: {
	  		  // eeprom conf loaded
	  		  log_message(STAT_EEPROM_LOADED, -1);
	  		  break;
	  	  }
	  }
#endif
  }
  else {
	  // eeprom init error, defaults loaded
	  load_eeprom_defaults(&loaded_config, &bb_num);
	  log_message(ERR_EEPROM_INIT, -1);
	  start_buzz_timer(500, UINT32_MAX, 1, 0);
  }
  bb_addr = loaded_config.bayboardIP;
  char logmsg[sizeof(BB_STAT_STARTING_IDENTIFY) + 3];
  snprintf(logmsg, sizeof(logmsg), BB_STAT_STARTING_IDENTIFY "%d", bb_num);
  log_message(logmsg, -1);

  log_message(STAT_VERSION_INFO, -1);

  // Init flash
  if(init_flash_logging(&hspi1, FLASH_CS_GPIO_Port, FLASH_CS_Pin)) {
	  start_led_timer(500, UINT32_MAX, 1);
  }

  /* USER CODE END RTOS_QUEUES */

  /* Create the thread(s) */
  /* creation of startTask */
  startTaskHandle = osThreadNew(StartAndMonitor, NULL, &startTask_attributes);

  /* USER CODE BEGIN RTOS_THREADS */
  /* add threads, ... */
  flashClearTaskHandle = osThreadNew(FlashClearTask, NULL, &flash_clear_task_attr);
  /* USER CODE END RTOS_THREADS */

  /* USER CODE BEGIN RTOS_EVENTS */
  /* add events, ... */
  /* USER CODE END RTOS_EVENTS */

  /* Start scheduler */
  osKernelStart();

  /* We should never get here as control is now taken by the scheduler */

  /* Infinite loop */
  /* USER CODE BEGIN WHILE */
  while (1)
  {
    /* USER CODE END WHILE */

    /* USER CODE BEGIN 3 */
  }
  /* USER CODE END 3 */
}

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
/* USER CODE BEGIN Header_StartAndMonitor */
/**
  * @brief  Function implementing the startTask thread.
  * @param  argument: Not used
  * @retval None
  */
/* USER CODE END Header_StartAndMonitor */
void StartAndMonitor(void *argument)
{
  /* init code for LWIP */
  MX_LWIP_Init();
  /* USER CODE BEGIN 5 */
  osDelay(1);

  	// Signal end of critical section

	if(is_net_logging_up()) {
		// No UDP error
		start_led_timer(1, 0, 0);
	}
	else {
		// UDP error
		start_led_timer(250, UINT32_MAX, 1);
	}

	//HAL_GPIO_WritePin(BUZZ_GPIO_Port, BUZZ_Pin, 1);
	start_buzz_timer(1000, 0, 0, 1);

    setup_system_state();

	// Config SR
  	Shift_Reg reg = {0};
  	reg.VLV_CTR_GPIO_Port = VLV_CTRL_GPIO_Port;
  	reg.VLV_CTR_GPIO_Pin = VLV_CTRL_Pin;
  	reg.VLV_CLK_GPIO_Port = BUFF_CLK_GPIO_Port;
  	reg.VLV_CLK_GPIO_Pin = BUFF_CLK_Pin;

  	VLV_Set_Conf(reg, loaded_config.vlv1_en, loaded_config.vlv1_v,
  				loaded_config.vlv2_en, loaded_config.vlv2_v,
				loaded_config.vlv3_en, loaded_config.vlv3_v,
				loaded_config.vlv4_en, loaded_config.vlv4_v,
				loaded_config.vlv5_en, loaded_config.vlv5_v);

  	// Load valve pins
  	setup_valve(0, VLV1_EN_GPIO_Port, VLV1_EN_Pin, VLV1_OLD_GPIO_Port, VLV1_OLD_Pin);
  	setup_valve(1, VLV2_EN_GPIO_Port, VLV2_EN_Pin, VLV2_OLD_GPIO_Port, VLV2_OLD_Pin);
  	setup_valve(2, VLV3_EN_GPIO_Port, VLV3_EN_Pin, VLV3_OLD_GPIO_Port, VLV3_OLD_Pin);
  	setup_valve(3, VLV4_EN_GPIO_Port, VLV4_EN_Pin, VLV4_OLD_GPIO_Port, VLV4_OLD_Pin);
  	setup_valve(4, VLV5_EN_GPIO_Port, VLV5_EN_Pin, VLV5_OLD_GPIO_Port, VLV5_OLD_Pin);

	// Init sensors and peripherals
  	// ADC
  	sensors_h.adc1_h.MAX11128_CS_PORT = ADC1_CS_GPIO_Port;
  	sensors_h.adc1_h.MAX11128_CS_ADDR = ADC1_CS_Pin;
  	sensors_h.adc1_h.HARDWARE_CONFIGURATION = NO_EOC_NOR_CNVST;
  	sensors_h.adc1_h.NUM_CHANNELS = 16;

  	sensors_h.adc2_h.MAX11128_CS_PORT = ADC2_CS_GPIO_Port;
  	sensors_h.adc2_h.MAX11128_CS_ADDR = ADC2_CS_Pin;
  	sensors_h.adc2_h.HARDWARE_CONFIGURATION = NO_EOC_NOR_CNVST;
  	sensors_h.adc2_h.NUM_CHANNELS = 16;

  	init_adc(&hspi4, &(sensors_h.adc1_h));
  	// Check to make sure the chip is connected
	uint16_t adc_values[16] = {0};
	read_adc(&hspi4, &(sensors_h.adc1_h), adc_values);
	if(adc_values[ADC1_3V3_BUS_I] == 0) { // 3v3 bus voltage should always be greater than 0
		// ADC1 error
		log_message(BB_ERR_ADC1_INIT, -1);
	}

  	init_adc(&hspi4, &(sensors_h.adc2_h));

  	// TC ADCs
  	ADS_configTC(&(sensors_h.TCs[0]), &hspi2, GPIOB, GPIO_PIN_14, PERIPHERAL_TIMEOUT, TC3_CS_GPIO_Port, TC3_CS_Pin, ADS_MUX_AIN0_AIN1, loaded_config.tc1_gain, ADS_DATA_RATE_600);
  	ADS_configTC(&(sensors_h.TCs[1]), &hspi2, GPIOB, GPIO_PIN_14, PERIPHERAL_TIMEOUT, TC3_CS_GPIO_Port, TC3_CS_Pin, ADS_MUX_AIN3_AIN2, loaded_config.tc2_gain, ADS_DATA_RATE_600);
  	ADS_configTC(&(sensors_h.TCs[2]), &hspi2, GPIOB, GPIO_PIN_14, PERIPHERAL_TIMEOUT, TC2_CS_GPIO_Port, TC2_CS_Pin, ADS_MUX_AIN0_AIN1, loaded_config.tc3_gain, ADS_DATA_RATE_600);
  	ADS_configTC(&(sensors_h.TCs[3]), &hspi2, GPIOB, GPIO_PIN_14, PERIPHERAL_TIMEOUT, TC2_CS_GPIO_Port, TC2_CS_Pin, ADS_MUX_AIN3_AIN2, loaded_config.tc4_gain, ADS_DATA_RATE_600);
  	ADS_configTC(&(sensors_h.TCs[4]), &hspi2, GPIOB, GPIO_PIN_14, PERIPHERAL_TIMEOUT, TC1_CS_GPIO_Port, TC1_CS_Pin, ADS_MUX_AIN0_AIN1, loaded_config.tc5_gain, ADS_DATA_RATE_600);
  	ADS_configTC(&(sensors_h.TCs[5]), &hspi2, GPIOB, GPIO_PIN_14, PERIPHERAL_TIMEOUT, TC1_CS_GPIO_Port, TC1_CS_Pin, ADS_MUX_AIN3_AIN2, loaded_config.tc6_gain, ADS_DATA_RATE_600);

  	if(ADS_init(&(sensors_h.tc_main_h), sensors_h.TCs, NUM_TCS)) {
  		// ADS thread start error
  		log_message(ERR_ADS_INIT_THREAD_ERR, -1);
  	}

  	// IMUs
  	sensors_h.imu1_h.hi2c = &hi2c5;
  	sensors_h.imu1_h.I2C_TIMEOUT = PERIPHERAL_TIMEOUT;
  	sensors_h.imu1_h.XL_x_offset = 0;
  	sensors_h.imu1_h.XL_y_offset = 0;
  	sensors_h.imu1_h.XL_z_offset = 0;
  	sensors_h.imu1_h.G_x_offset = 0;
  	sensors_h.imu1_h.G_y_offset = 0;
  	sensors_h.imu1_h.G_z_offset = 0;
  	sensors_h.imu1_h.SA0 = 0;

  	sensors_h.imu2_h.hi2c = &hi2c5;
  	sensors_h.imu2_h.I2C_TIMEOUT = PERIPHERAL_TIMEOUT;
  	sensors_h.imu2_h.XL_x_offset = 0;
  	sensors_h.imu2_h.XL_y_offset = 0;
  	sensors_h.imu2_h.XL_z_offset = 0;
  	sensors_h.imu2_h.G_x_offset = 0;
  	sensors_h.imu2_h.G_y_offset = 0;
  	sensors_h.imu2_h.G_z_offset = 0;
  	sensors_h.imu2_h.SA0 = 1;

  	if(IMU_init(&(sensors_h.imu1_h)) == -1) {
  		// IMU 1 init error
  		log_message(ERR_IMU_INIT "1", -1);
  	}
  	if(IMU_init(&(sensors_h.imu2_h)) == -1) {
  		// IMU 2 init error
  		log_message(ERR_IMU_INIT "2", -1);
  	}

  	// Barometers
  	sensors_h.bar1_h.hspi = &hspi6;
  	sensors_h.bar1_h.SPI_TIMEOUT = PERIPHERAL_TIMEOUT;
  	sensors_h.bar1_h.CS_GPIO_Port = BAR1_CS_GPIO_Port;
  	sensors_h.bar1_h.CS_GPIO_Pin = BAR1_CS_Pin;
  	sensors_h.bar1_h.pres_offset = 0;
  	sensors_h.bar1_h.alt_offset = 0;

  	sensors_h.bar2_h.hspi = &hspi6;
  	sensors_h.bar2_h.SPI_TIMEOUT = PERIPHERAL_TIMEOUT;
  	sensors_h.bar2_h.CS_GPIO_Port = BAR2_CS_GPIO_Port;
  	sensors_h.bar2_h.CS_GPIO_Pin = BAR2_CS_Pin;
  	sensors_h.bar2_h.pres_offset = 0;
  	sensors_h.bar2_h.alt_offset = 0;

  	if(MS5611_Reset(&(sensors_h.bar1_h))) {
  		// Bar 1 init error
  		log_message(ERR_BAR_INIT "1", -1);
  	}
  	MS5611_readPROM(&(sensors_h.bar1_h), &(sensors_h.prom1));
  	
  	if(MS5611_Reset(&(sensors_h.bar2_h))) {
  		// Bar 2 init error
  		log_message(ERR_BAR_INIT "2", -1);
  	}
  	MS5611_readPROM(&(sensors_h.bar2_h), &(sensors_h.prom2));

	// Start tasks

  	// Start telemetry sending over UDP
  	telemetrySendTaskHandle = osThreadNew(TelemetrySend, NULL, &telemetry_send_task_attr);

  	// Start telemetry task
  	telemetryTaskHandle = osThreadNew(TelemetryTask, NULL, &telemetry_task_attr);

  	// Start packet handler
  	packetTaskHandle = osThreadNew(ProcessPackets, NULL, &packet_task_attr);

  	// Start TCP client
  	switch(client_init(&loaded_config.flightcomputerIP, netif_is_link_up(&gnetif))) {
  		case 2: {
  			// threads didn't start
  			log_message(BB_ERR_TCP_CLIENT_INIT_THREAD, -1);
  			break;
  		}
  		case 1: {
  			// memory error
  			log_message(BB_ERR_TCP_CLIENT_INIT_MEM_ERR, -1);
  			break;
  		}
  		default: {
  			// client initialized
  			log_message(BB_STAT_TCP_CLIENT_INIT, -1);
  			break;
  		}
  	}

	// log startup done
	log_message(STAT_STARTUP_DONE, -1);

	/*
	 * ALL VALVE STATES SHOULD BE SENT ON THE START OF CONNECTION WITH LIMEWIRE (FC FOR BBs) (WHEN THE FC CONNECTS TO LIMEWIRE SEND THE VALVE STATES FOR THE ENTIRE ROCKET)
	 *
	 * fc telemetry comes from struct, sent on a 50hz loop
	 * bb telemetry comes from tcp packets, relayed to limewire and stored for optional access in autosequences
	 * fc valve states are sent after valve commands are sent AND possibly every now and then, in case something gets disconnected, then stored for optional access
	 * bb valve states are relayed from tcp packets, and saved for optional access
	 * all valve commands are processed when received. fc relays commands from limewire to bb
	 *
	 * telemetry task - read from peripherals and send telemetry msg
	 * tcp process task - process incoming packets for relaying or valve stuff
	 */

	uint8_t telemcounter = 0;
	uint8_t statecounter = 0;

	uint8_t fcconnected = 0;

	uint32_t startTick = HAL_GetTick();
	uint8_t logdelay = 0; // This is to delay the logging for 1 second after startup to let the link come online so the operators can read event messages from startup

	/* Infinite loop */
	for(;;) {
		//size_t freemem = xPortGetFreeHeapSize();
		if(logdelay > 4) {
			handle_logging(); // Log to UDP and flash
		}

		if(HAL_GetTick() - startTick > 250) {
			startTick = HAL_GetTick();
			if(logdelay < 5) {
				logdelay++;
			}

			if(telemcounter == 0) {
				log_telemetry();
				telemcounter = 0; // 4hz
			}
			else {
				telemcounter--;
			}

			if(statecounter == 0) {
				log_valve_states();
				statecounter = 1; // 2hz
			}
			else {
				statecounter--;
			}

			//size_t freemem = xPortGetFreeHeapSize();
			refresh_log_timers();

			int constat = is_client_connected();
			if(constat > -1) {
				if(fcconnected == 0 && constat == 1) {
					uint64_t valvetime = get_rtc_time();
			  	  	if(xSemaphoreTake(Board_h.bbValve_access, 5) == pdPASS) {
			  	  		Valve_State_t vstates[NUM_VALVE_CHS];
						for(int i = 0;i < NUM_VALVE_CHS;i++) {
							vstates[i] = Board_h.bbValveStates[i];
						}
			  	  		xSemaphoreGive(Board_h.bbValve_access);
						for(int i = 0;i < NUM_VALVE_CHS;i++) {
							Message statemsg = {0};
							statemsg.type = MSG_VALVE_STATE;
							statemsg.data.valve_state.timestamp = valvetime;
							statemsg.data.valve_state.valve_id = generate_valve_id(bb_num, i);
							statemsg.data.valve_state.valve_state = vstates[i];
							send_msg_to_device(&statemsg, 5);
						}
			  	  	}
				}
				fcconnected = constat;
			}
		}

	  osDelay(5);
	}
  /* USER CODE END 5 */
}
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

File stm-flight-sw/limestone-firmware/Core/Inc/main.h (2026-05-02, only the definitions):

#define TCP_PORT			5000
#define TELEMETRY_HZ		(uint32_t)50
#define FC_EEPROM_LEN		(uint16_t)100
#define EEPROM_RESTART_DELAY_MS				500
#define FC_EEPROM_PT_ZERO_DEFAULT			0.5
#define FC_EEPROM_PT_RANGE_DEFAULT			5000
#define FC_EEPROM_PT_MAX_DEFAULT			4.5
#define FC_EEPROM_TC_GAIN_DEFAULT			0x00
#define FC_EEPROM_VLV_VOL_DEFAULT			0x01
#define FC_EEPROM_VLV_EN_DEFAULT			0x01
#define FC_EEPROM_LIMEWIREIP_DEFAULT_1		141
#define FC_EEPROM_LIMEWIREIP_DEFAULT_2		212
#define FC_EEPROM_LIMEWIREIP_DEFAULT_3		192
#define FC_EEPROM_LIMEWIREIP_DEFAULT_4		160
#define FC_EEPROM_FCIP_DEFAULT_1			141
#define FC_EEPROM_FCIP_DEFAULT_2			212
#define FC_EEPROM_FCIP_DEFAULT_3			192
#define FC_EEPROM_FCIP_DEFAULT_4			170
#define FC_EEPROM_BB1IP_DEFAULT_1			141
#define FC_EEPROM_BB1IP_DEFAULT_2			212
#define FC_EEPROM_BB1IP_DEFAULT_3			192
#define FC_EEPROM_BB1IP_DEFAULT_4			180
#define FC_EEPROM_BB2IP_DEFAULT_1			141
#define FC_EEPROM_BB2IP_DEFAULT_2			212
#define FC_EEPROM_BB2IP_DEFAULT_3			192
#define FC_EEPROM_BB2IP_DEFAULT_4			190
#define FC_EEPROM_BB3IP_DEFAULT_1			141
#define FC_EEPROM_BB3IP_DEFAULT_2			212
#define FC_EEPROM_BB3IP_DEFAULT_3			192
#define FC_EEPROM_BB3IP_DEFAULT_4			200
#define FC_EEPROM_FRIP_DEFAULT_1			141
#define FC_EEPROM_FRIP_DEFAULT_2			212
#define FC_EEPROM_FRIP_DEFAULT_3			192
#define FC_EEPROM_FRIP_DEFAULT_4			210
#define FC_EEPROM_OX_MPV_DEFAULT			0
#define FC_EEPROM_FUEL_MPV_DEFAULT			1
#define FC_EEPROM_PILOT_DEFAULT				0
#define FC_EEPROM_DROGUE_DEFAULT			1
#define FC_EEPROM_MAIN_DEFAULT				2
#define FC_EEPROM_FUEL_ISO_DEFAULT			1
#define FC_EEPROM_OX_ISO_DEFAULT			0
#define FC_MAC_ADDR_1		0x00
#define FC_MAC_ADDR_2		0x80
#define FC_MAC_ADDR_3		0xE1
#define FC_MAC_ADDR_4		0x3f
#define FC_MAC_ADDR_5		0xd8
#define FC_MAC_ADDR_6		0xa2
#define FLASH_TELEM_MARK	(uint8_t)0x1D
#define FLASH_MSG_MARK		(uint8_t)0x1E
#define FLASH_BOTH_MARK		(uint8_t)0x1F
#define ERROR_UDP_PORT		(uint16_t)1234
#define TELEM_UDP_PORT		(uint16_t)6767
#define RADIO_PACKET_LENGTH		49
#define ERROR_MSG_TYPES		(size_t)32 // Should be a multiple of 2
#define PERI_ERROR_MSG_TYPES	(size_t)8
#define ERROR_THROTTLE_MAX		10 // Not more than 15
#define SHUNT_RES_20M		(uint16_t)20
#define SHUNT_RES_2M		(uint16_t)2
#define VALVE_SHUNT_RES		SHUNT_RES_20M
#define POWER_SHUNT_3V3_5V	SHUNT_RES_20M
#define POWER_SHUNT_12V_24V SHUNT_RES_2M
#define POWER_24V_RES_A		(uint32_t)100000
#define POWER_24V_RES_B		(uint32_t)14300
#define POWER_12V_RES_A		(uint32_t)100000
#define POWER_12V_RES_B		(uint32_t)33200
#define POWER_5V_RES_A		(uint32_t)10000
#define POWER_5V_RES_B		(uint32_t)15000
#define POWER_3V3_RES_A		(uint32_t)1000
#define POWER_3V3_RES_B		(uint32_t)10000
#define ADC_3V3_BUS_I		(size_t)0
#define ADC_VLV1_CURRENT_I	(size_t)1
#define ADC_VLV2_CURRENT_I	(size_t)2
#define ADC_VLV3_CURRENT_I	(size_t)3
#define ADC_PT1_I			(size_t)4
#define ADC_PT2_I			(size_t)5
#define ADC_PT3_I			(size_t)6
#define ADC_PT4_I			(size_t)7
#define ADC_PT5_I			(size_t)8
#define ADC_24V_CURRENT_I	(size_t)9
#define ADC_12V_CURRENT_I	(size_t)10
#define ADC_5V_CURRENT_I	(size_t)11
#define ADC_3V3_CURRENT_I	(size_t)12
#define ADC_5V_BUS_I		(size_t)13
#define ADC_12V_BUS_I		(size_t)14
#define ADC_24V_BUS_I		(size_t)15
#define FLUCTUS_APOGEE_CHANNEL		ADC_PT5_I
#define FLUCTUS_5K_CHANNEL			ADC_PT4_I
#define FLUCTUS_1K_CHANNEL			ADC_PT3_I
#define DIVIDER_VALVE		(uint8_t)1
#define DIVIDER_12V_24V		(uint8_t)0
#define DIVIDER_3V3_5V		(uint8_t)1
#define PERIPHERAL_TIMEOUT		10
#define GPS_NRST_Pin GPIO_PIN_4
#define GPS_NRST_GPIO_Port GPIOE
#define RF_DIO3_Pin GPIO_PIN_13
#define RF_DIO3_GPIO_Port GPIOC
#define RF_DIO2_Pin GPIO_PIN_14
#define RF_DIO2_GPIO_Port GPIOC
#define RF_DIO1_Pin GPIO_PIN_15
#define RF_DIO1_GPIO_Port GPIOC
#define RADIO_CS_Pin GPIO_PIN_6
#define RADIO_CS_GPIO_Port GPIOF
#define RF_BUSY_Pin GPIO_PIN_10
#define RF_BUSY_GPIO_Port GPIOF
#define RF_MODE_SW_Pin GPIO_PIN_0
#define RF_MODE_SW_GPIO_Port GPIOC
#define RF_NSRT_Pin GPIO_PIN_2
#define RF_NSRT_GPIO_Port GPIOC
#define BAR2_CS_Pin GPIO_PIN_3
#define BAR2_CS_GPIO_Port GPIOA
#define BAR1_CS_Pin GPIO_PIN_4
#define BAR1_CS_GPIO_Port GPIOA
#define ETH_NRST_Pin GPIO_PIN_0
#define ETH_NRST_GPIO_Port GPIOB
#define PDB_DIO1_Pin GPIO_PIN_14
#define PDB_DIO1_GPIO_Port GPIOF
#define PDB_DIO2_Pin GPIO_PIN_15
#define PDB_DIO2_GPIO_Port GPIOF
#define ADC_CS_Pin GPIO_PIN_11
#define ADC_CS_GPIO_Port GPIOE
#define VLV2_OLD_Pin GPIO_PIN_15
#define VLV2_OLD_GPIO_Port GPIOE
#define TC1_CS_Pin GPIO_PIN_9
#define TC1_CS_GPIO_Port GPIOD
#define TC2_CS_Pin GPIO_PIN_10
#define TC2_CS_GPIO_Port GPIOD
#define VLV3_EN_Pin GPIO_PIN_8
#define VLV3_EN_GPIO_Port GPIOG
#define VLV1_EN_Pin GPIO_PIN_6
#define VLV1_EN_GPIO_Port GPIOC
#define VLV3_OLD_Pin GPIO_PIN_7
#define VLV3_OLD_GPIO_Port GPIOC
#define VLV1_OLD_Pin GPIO_PIN_8
#define VLV1_OLD_GPIO_Port GPIOC
#define VLV2_EN_Pin GPIO_PIN_8
#define VLV2_EN_GPIO_Port GPIOA
#define BUFF_CLR_Pin GPIO_PIN_9
#define BUFF_CLR_GPIO_Port GPIOA
#define BUFF_CLK_Pin GPIO_PIN_10
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

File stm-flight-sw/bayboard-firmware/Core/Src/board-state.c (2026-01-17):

/*
 * board-state.c
 *
 *  Created on: Nov 9, 2025
 *      Author: felix
 */

#include "board-state.h"

Board_State_t Board_h = {0};

void setup_system_state() {
	// Init rocket state struct
	memset(&Board_h, 0, sizeof(Board_h)); // Reset contents
	Board_h.bbState_access = xSemaphoreCreateMutex();
	Board_h.bbValve_access = xSemaphoreCreateMutex();
}

void setup_valve(uint8_t index, GPIO_TypeDef * EN_Port, uint16_t EN_Pin, GPIO_TypeDef * OLD_Port, uint16_t OLD_Pin) {
	Board_h.bbValves[index].VLV_EN_GPIO_Port = EN_Port;
	Board_h.bbValves[index].VLV_EN_GPIO_Pin = EN_Pin;
	Board_h.bbValves[index].VLV_OLD_GPIO_Port = OLD_Port;
	Board_h.bbValves[index].VLV_OLD_GPIO_Pin = OLD_Pin;
	Board_h.bbValveStates[index] = VLV_State(Board_h.bbValves[index]);
}

// Pack telemetry message
// returns 0 if successful, 1 if the telemetry data could not be accessed
// timeout_ticks: how many FreeRTOS ticks to wait before giving up
int pack_bb_telemetry_msg(TelemetryMessage *msg, uint64_t timestamp, uint8_t timeout_ticks) {
	msg->board_id = bb_num;
	msg->num_channels = BB1_TELEMETRY_CHANNELS; // all the bay boards have the same number of channels
	msg->timestamp = timestamp;
	if(xSemaphoreTake(Board_h.bbState_access, timeout_ticks) == pdPASS) {
		msg->telemetry_data[BB1_VLV1_CURRENT_I] 	= Board_h.bbState.vlv1_current;
		msg->telemetry_data[BB1_VLV1_OLD_I] 		= Board_h.bbState.vlv1_old;
		msg->telemetry_data[BB1_VLV2_CURRENT_I] 	= Board_h.bbState.vlv2_current;
		msg->telemetry_data[BB1_VLV2_OLD_I] 		= Board_h.bbState.vlv2_old;
		msg->telemetry_data[BB1_VLV3_CURRENT_I] 	= Board_h.bbState.vlv3_current;
		msg->telemetry_data[BB1_VLV3_OLD_I] 		= Board_h.bbState.vlv3_old;
		msg->telemetry_data[BB1_VLV4_CURRENT_I] 	= Board_h.bbState.vlv4_current;
		msg->telemetry_data[BB1_VLV4_OLD_I] 		= Board_h.bbState.vlv4_old;
		msg->telemetry_data[BB1_VLV5_CURRENT_I] 	= Board_h.bbState.vlv5_current;
		msg->telemetry_data[BB1_VLV5_OLD_I] 		= Board_h.bbState.vlv5_old;
		msg->telemetry_data[BB1_VLV6_CURRENT_I] 	= Board_h.bbState.vlv6_current;
		msg->telemetry_data[BB1_VLV6_OLD_I] 		= Board_h.bbState.vlv6_old;
		msg->telemetry_data[BB1_VLV7_CURRENT_I] 	= Board_h.bbState.vlv7_current;
		msg->telemetry_data[BB1_VLV7_OLD_I] 		= Board_h.bbState.vlv7_old;
		msg->telemetry_data[BB1_PT_1_I] 			= Board_h.bbState.pt1;
		msg->telemetry_data[BB1_PT_2_I] 			= Board_h.bbState.pt2;
		msg->telemetry_data[BB1_PT_3_I] 			= Board_h.bbState.pt3;
		msg->telemetry_data[BB1_PT_4_I] 			= Board_h.bbState.pt4;
		msg->telemetry_data[BB1_PT_5_I] 			= Board_h.bbState.pt5;
		msg->telemetry_data[BB1_PT_6_I] 			= Board_h.bbState.pt6;
		msg->telemetry_data[BB1_PT_7_I] 			= Board_h.bbState.pt7;
		msg->telemetry_data[BB1_PT_8_I] 			= Board_h.bbState.pt8;
		msg->telemetry_data[BB1_PT_9_I] 			= Board_h.bbState.pt9;
		msg->telemetry_data[BB1_PT_10_I] 			= Board_h.bbState.pt10;
		msg->telemetry_data[BB1_TC_1_I] 			= Board_h.bbState.tc1;
		msg->telemetry_data[BB1_TC_2_I] 			= Board_h.bbState.tc2;
		msg->telemetry_data[BB1_TC_3_I] 			= Board_h.bbState.tc3;
		msg->telemetry_data[BB1_TC_4_I] 			= Board_h.bbState.tc4;
		msg->telemetry_data[BB1_TC_5_I] 			= Board_h.bbState.tc5;
		msg->telemetry_data[BB1_TC_6_I] 			= Board_h.bbState.tc6;
		msg->telemetry_data[BB1_IMU1_X_I] 			= Board_h.bbState.imu1_A.XL_x;
		msg->telemetry_data[BB1_IMU1_Y_I] 			= Board_h.bbState.imu1_A.XL_y;
		msg->telemetry_data[BB1_IMU1_Z_I] 			= Board_h.bbState.imu1_A.XL_z;
		msg->telemetry_data[BB1_IMU1_WP_I] 			= Board_h.bbState.imu1_W.G_y;
		msg->telemetry_data[BB1_IMU1_WR_I] 			= Board_h.bbState.imu1_W.G_x;
		msg->telemetry_data[BB1_IMU1_WY_I] 			= Board_h.bbState.imu1_W.G_z;
		msg->telemetry_data[BB1_IMU2_X_I] 			= Board_h.bbState.imu2_A.XL_x;
		msg->telemetry_data[BB1_IMU2_Y_I] 			= Board_h.bbState.imu2_A.XL_y;
		msg->telemetry_data[BB1_IMU2_Z_I] 			= Board_h.bbState.imu2_A.XL_z;
		msg->telemetry_data[BB1_IMU2_WP_I] 			= Board_h.bbState.imu2_W.G_y;
		msg->telemetry_data[BB1_IMU2_WR_I] 			= Board_h.bbState.imu2_W.G_x;
		msg->telemetry_data[BB1_IMU2_WY_I] 			= Board_h.bbState.imu2_W.G_z;
		msg->telemetry_data[BB1_BAR_1_I] 			= Board_h.bbState.bar1;
		msg->telemetry_data[BB1_BAR_2_I] 			= Board_h.bbState.bar2;
		msg->telemetry_data[BB1_24V_VOLTAGE_I] 		= Board_h.bbState.bus24v_voltage;
		msg->telemetry_data[BB1_24V_CURRENT_I] 		= Board_h.bbState.bus24v_current;
		msg->telemetry_data[BB1_12V_VOLTAGE_I] 		= Board_h.bbState.bus12v_voltage;
		msg->telemetry_data[BB1_12V_CURRENT_I] 		= Board_h.bbState.bus12v_current;
		msg->telemetry_data[BB1_5V_VOLTAGE_I] 		= Board_h.bbState.bus5v_voltage;
		msg->telemetry_data[BB1_5V_CURRENT_I] 		= Board_h.bbState.bus5v_current;
		msg->telemetry_data[BB1_3V3_VOLTAGE_I] 		= Board_h.bbState.bus3v3_voltage;
		msg->telemetry_data[BB1_3V3_CURRENT_I] 		= Board_h.bbState.bus3v3_current;
		msg->telemetry_data[BB1_BOARD_TEMP_I]		= Board_h.bbState.board_temp;
		xSemaphoreGive(Board_h.bbState_access);
	}
	else {
		return 1;
	}

	return 0;
}
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

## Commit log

2024-09-06 The great avionics code consolidation
    [data.csv]
2024-09-22 Added valve driver template and started limestone template
2024-09-26 progress on FC template
    [data.csv]
2024-10-06 Adding old bootloader firmware
    [JLCPCB-BOM.csv, ethernet.sch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]
2024-10-20 Update Board Drivers README
2024-10-20 update drivers README with correct ADS1120 SPI Bus
2024-11-25 Added boilerplate source files for ADS1120 driver
2025-01-09 Thermocouple driver progress
2025-01-11 Valve driver start
2025-01-12 More copy-paste boiler plate
2025-01-12 Added write, read, reset
    [MS5611.c]
2025-01-13 Reorganized some things
    [JLCPCB-BOM.csv, data1.csv, ethernet.sch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]
2025-01-13 Fixed up driver README(s)
    [FCBBADC.c, STM32_Nucleo_H723ZG_ETH.ioc, main.c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]
2025-01-15 ADS1120 thermocouple polynomial and driver redesign
    [ADS1120.c]
2025-01-18 prints out height data at regular intervals
2025-01-18 pressure and temperature calculation for the MS5611
2025-01-19 valve open load detection start
    [JLCPCB-BOM.csv, ethernet.sch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]
2025-01-26 Updated Valve driver and MS5611
2025-01-26 press p in the command line to see real-time pressure
2025-02-09 switched to C++
2025-02-09 Kalman filter skeleton
    This code first initializes the noise covariance matrix for all the three sensors fused together (barometer, IMU, GPS) based on their spec sheets and then do the standard Kalman filter steps. However it is not very correct because the ideal method should be to use one of Barometer+IMU, GPS+IMU or barometer+GPS sensor fusion combination, depending on which two sensors are the most reliable. Unless it is feasible in other ways
2025-02-10 Update Kalman_rocket_apogee.cpp
    Revision: Actually multiple measurements (e.g. all 3 types of sensors) can be integrated, however the code is not correct for it
2025-02-10 Update Kalman_rocket_apogee.cpp
    This code first initializes the noise covariance matrix for all the three sensors (barometer, IMU, GPS) based on their spec sheets and then do the standard Kalman filter steps to fuse them together. However it is not very correct. Please refer to Static Estimation – Multiple Measurements of Kalman filter.
2025-02-10 Update Kalman_rocket_apogee.cpp
    This code first initializes the noise covariance matrix for all the three sensors (barometer, IMU, GPS) based on their spec sheets and then do the standard Kalman filter steps to fuse them together. However it is not very correct. Please refer to Static Estimation – Multiple Measurements for Kalman filter to revise it.
2025-02-11 ADS1120 driver progress/switch to async structure
2025-03-02 Add dev board pinout to M24256E README.md
2025-03-22 Add new version of M24256E drivers
2025-03-31 Add documentation to all function prototypes in M24256E.h
2025-04-06 Adding an IMU monitor to trigger the Apogee task
2025-04-13 Added random, but correctly parsed, responses
    [main.c]
2025-04-21 Added SPI setup to TC driver documentation
2025-04-23 old SX1280 driver
2025-04-27 Include only main.h in EEPROM driver
2025-04-27 Implement rest of read functions for EEPROM driver
2025-05-01 Fix endianness of address in mem write buffers
    [M24256E.c]
2025-05-01 Fix error checking for invalid addresses
    [M24256E.c]
2025-05-01 Fix a couple bugs in EEPROM functions
    [M24256E.c]
2025-06-02 Redid a lot of SEB but still not working
    [main.c, main.h]
2025-06-23 Created limestone-firmware project
    [data.csv]
2025-07-04 Updated valve driver - now supports bay boards and better open load detection
2025-07-06 Updated IMU driver to support multiple addresses and added current sensing and PT math to limestone-firmware
2025-07-06 Fixed type issues with RTC and got the time synchronization down to under 1ms
    [main.c]
2025-07-10 new branch for IMU update
2025-07-11 Fixed a stupid issue where the ethernet task doesn't have enough stack
    [limestone-firmware.ioc, main.c]
2025-07-12 new thrust curve file
2025-07-17 Packet handler done. Limestone firmware is now usable for testing (still needs a lot of error handling work)
    [main.c]
2025-07-19 Flash and UDP logging of error messages done. Also fixed a timing issue with the MS5611 driver.
    [ADS1120.c, M24256E.c, MS5611.c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]
2025-07-29 TCP server error handling started - listening thread done
    [M24256E.c, W25N04KV.c, main.c]
2025-08-02 TCP server error handling and logging done!
    [main.h]
2025-08-08 Startup error handling and logging done
    [limestone-firmware.ioc, main.c, main.h]
2025-08-10 FC firmware error logging done
    [LSM6DSO32XTR.c, MS5611.c, main.c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]
2025-08-11 Device commands implemented
2025-08-11 Fixed a stupid problem
    [main.c]
2025-08-15 TCP client mostly done + a couple bug fixes
    [bayboard-firmware.ioc, limestone-firmware.ioc, main.c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]
2025-08-16 TCP client done, bay board firmware 50% ported
2025-08-18 Bay Board firmware working + a very weird STM bug fixed
    [bayboard-firmware.ioc, limestone-firmware.ioc, main.c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]
2025-09-02 Reorg :)
    [data.csv, data1.csv]
2025-09-21 Comment out unnecessary IMU class.
    IMU class in noise_generator.hpp was preventing compilation because
    of unused variables. Not needed currently, so commented out.
2025-09-21 feat(sx1280): initialize new FreeRTOS-compliant driver structure
    Replaces the entire previous driver structure with a new structure.
    designed to meet the requirements outlined in the Radio Firmware Project Spec:
    - clean, high-level API
    - thread-safe SPI wrapper using FreeRTOS critical sections.
    [SX1280.c]
2025-09-22 feat(sx1280): initialize new FreeRTOS-compliant driver structure
2025-09-22 Major board comms fixes
    [M24256E.c, bayboard-firmware.ioc, limestone-firmware.ioc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]
2025-09-28 Fixed sym links for firmware projects and added FC support for PDB control
    [main.c]
2025-10-08 Finishing up functions
    This is finishing up most functions as well as adding in other missing function prototypes (most to be reviewed).
    [SX1280.c]
2025-10-19 Fixes to typos in functions
    Fixing typos that was creating compilation errors
    [SX1280.c]
2025-10-26 added driver
2025-10-26 Updates to sx1280 drivers
    Removes the IRQ handling and made some major fixes to the functions. The SetTx functions were set up incorrectly.
    [SX1280.c]
2025-10-26 Fixes to comments
    Fixes to informal comments
    [SX1280.c]
2025-10-26 Made directory and LED blinking in state 0
2025-10-28 Update SX1280.c
    Replace HAL_Delay with vTaskDelay for RTOS compatibility
    [SX1280.c]
2025-10-28 Update SX1280.c
    Fix to setting Tx params
    [SX1280.c]
2025-10-29 programming FSM structure and first couple states
2025-11-01 New sx1280 driver datasheet
2025-11-01 Update to drivers
    This is an update to the drivers accounting for the new SX1280 datasheet revision.
2025-11-02 Bay Board refactor progress
2025-11-04 rewrote state machine using switch statements
2025-11-09 Bay Board firmware refactoring done
2025-11-11 minor update to SX1280 firmware
    This is just minor fixes to the comments in the driver code, as well as further testing of the hardware.
    [SX1280.c, main.c]
2025-11-14 Converted versioning to a shell script, progress on LMP device command ACKs
2025-11-17 Add build info device command
2025-11-17 Added board temp telemetry channel
2025-11-17 Add device command ACKs to flash clearing
2025-11-18 Updates to radio driver and main.c
    These are big updates to how we transmit, test code for main.c, and reformatting.
2025-11-30 Device command fixes
2025-12-02 ground states work correctly, incorporating apogee detection
    [main.c]
2025-12-06 LMP changes done + small bug fixes
    [eeprom-config.c, main.c]
2025-12-27 wrote filter
2025-12-28 debugged, implementing filter in autosequence script
2025-12-29 added velocity and orientation buffer, need to implement and update timers
2026-01-03 Fixed an issue with error logging number codes
    [LSM6DSO32XTR.h]
2026-01-08 Bay Board ntp script too
2026-01-12 Heartbeats and valve states every second
2026-01-17 Attempts to fix FC crashing. Saving before changing clock config.
    [ADS1120.c, bayboard-firmware.ioc, limestone-firmware.ioc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]
2026-01-17 Hopefully fixed timing issues
    [ADS1120.c, LSM6DSO32XTR.c, MAX11128.c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]
2026-01-19 Shakedown 2, flash broken
    [ADS1120.c, LSM6DSO32XTR.c, MAX11128.c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]
2026-01-25 Fixed most issues, flash still broken
    [W25N04KV.c, limestone-firmware.ioc]
2026-01-25 added simple curve fit to model altitude readings and determine acceleration, velocity, and altitude post-lockout
2026-01-31 Flash driver fixed, 1st Coldflow
    [W25N04KV.c]
2026-02-13 Memory progress - still unstable
    [limestone-firmware.ioc, main.c]
2026-02-13 LWIP and FreeRTOS config fixed
    [bayboard-firmware.ioc, limestone-firmware.ioc]
2026-02-13 Added malloc hooks to make malloc and free thread safe
2026-02-19 added timer logic & comments
2026-03-12 small bug fixes, working on synthetic testing
    [target_flight_data-apogee_12000.0.csv]
2026-03-19 Fix flash for bay boards too
    [W25N04KV.c]
2026-03-20 minor bug fixes in ad-functions, bug fix for quadr_curve_fit, reordering of lapse rate / chute deploy pressure & small variable type changes in autosequence-script, added flight states in flight-auto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
2026-03-21 GPS changes, lots of small fixes, coldflow ready flight-autosequence
    [main.c, main.h]
2026-04-10 Change ground station MAC address
2026-04-10 Actually change ground station MAC
2026-04-12 csv parser c
    [target_flight_data-apogee_12000.0.csv]
2026-04-12 added a few things here and there, need to see whether changing it from 50ms per to 20ms per breaks anything/anything needs to be changed as a result
    [target_flight_data-apogee_12000.0.csv]
2026-04-12 Revert "csv parser c"
    This reverts commit 06b7f978f1f1e780c379c360bba4158bb2e5a933.
    [target_flight_data-apogee_12000.0.csv]
2026-04-16 testing autosequence on lm3 data
    [flightData_lm3.csv, target_flight_data-apogee_12000.0.csv]
2026-04-20 Flash driver fixes and autosequence boot parameters
    [W25N04KV.c, eeprom-config.c, flash.c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]
2026-04-23 debugged through april launch data, will read previous data next
    [launch_04_09_2026.csv]
2026-04-23 autosequence works for pf2 data as well
    [launch_04_09_2026.csv]
2026-05-02 Force dome isos open during autosequence, added recovery pressure to radio
2026-05-08 Merge pull request #27 from masa-umich/autosequence-test
    Final Autosequence Changes with Changes made from PR suggestions
    [launch_04_09_2026.csv, sim_sensor_data.csv, sim_sensor_data_old.csv]
2026-05-13 Lower radio transmit power and duty cycle to prevent overheating
    [SX1280.c]

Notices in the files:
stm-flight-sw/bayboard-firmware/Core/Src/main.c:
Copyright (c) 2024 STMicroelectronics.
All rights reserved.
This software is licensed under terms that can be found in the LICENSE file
